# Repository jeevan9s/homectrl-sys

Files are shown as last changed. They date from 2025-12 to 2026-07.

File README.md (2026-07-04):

# homectrl

Home-automation controller with a Next.js dashboard. 

 ### Status
>- Controller PCB currently being manufactures
>- Firmware and **docs development** in progress.
>- Mechanical components currently being printed.

<details>
<summary><strong>Table of Contents</strong></summary>

- [homectrl](#homectrl)
    - [Status](#status)
  - [Overview](#overview)
  - [Features](#features)
    - [Controller](#controller)
    - [App](#app)
    - [Mechanical](#mechanical)
  - [Architecture](#architecture)
    - [Systems](#systems)
  - [Electrical](#electrical)
    - [Power System](#power-system)
    - [Microcontroller](#microcontroller)
    - [Pump Interface](#pump-interface)
    - [Stepper Motor Interface](#stepper-motor-interface)
    - [Peripheral Devices](#peripheral-devices)
  - [Mechanical](#mechanical-1)
    - [Container](#container)
    - [Lid](#lid)
  - [Firmware](#firmware)
  - [Web-App](#web-app)
  - [Repository Structure](#repository-structure)
  - [Gallery](#gallery)

</details>

I built homectrl because I wanted to automate my first apartment. 

<table> 
  <tr> 
    <td width="50%"> 
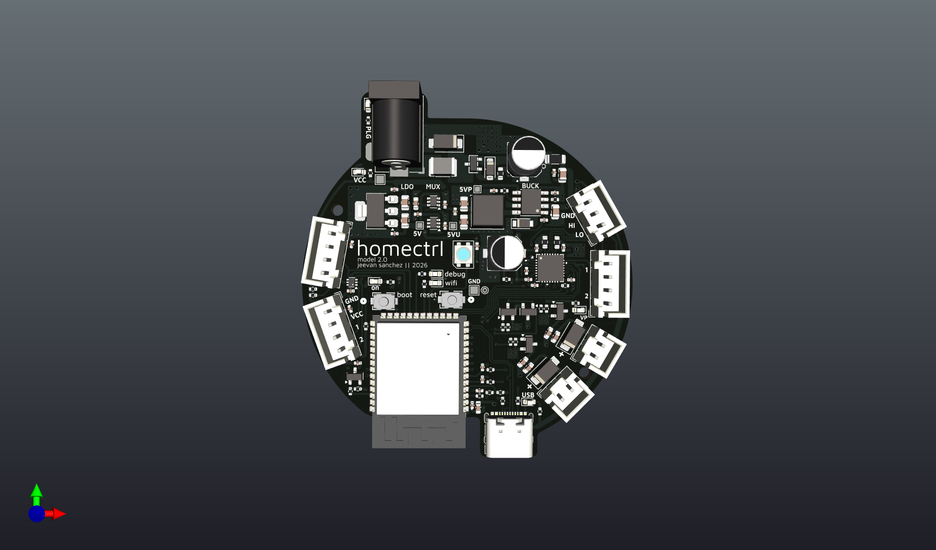
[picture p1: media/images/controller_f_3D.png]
       
    </td> 
    <td width="50%"> 
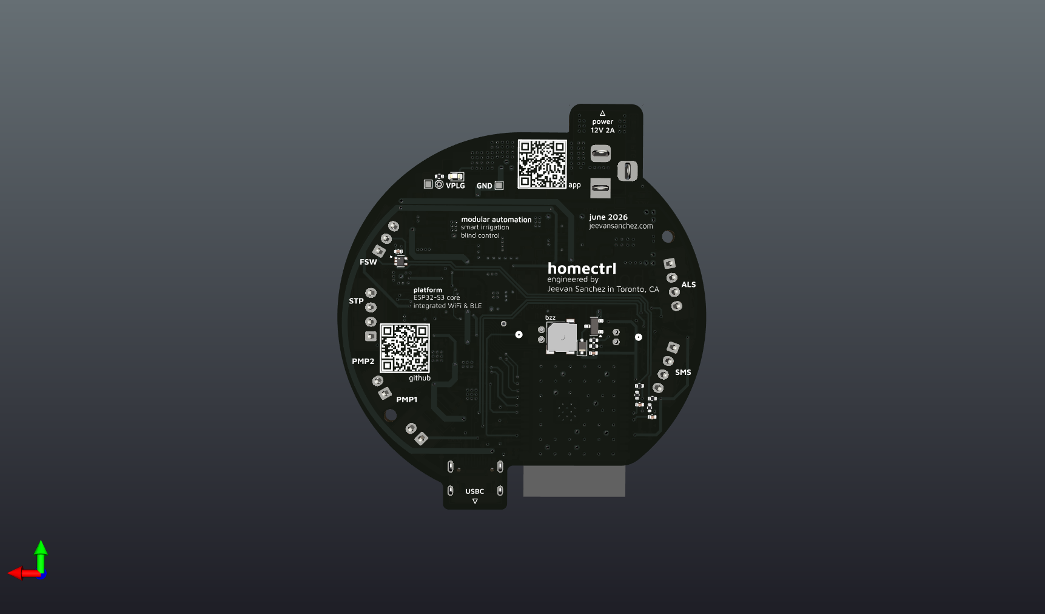
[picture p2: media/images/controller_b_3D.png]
       
    </td> 
  </tr> 
</table>

## Overview
Practicality is a consistent motive when building. 

As I moved into my first apartment during my first year at Queen's University, I wanted a device capable of smart-control for plants and window blinds, which are main components of my studio. This pushed me to build **homectrl**, a controller that leverages sensor readings, actuators, and WiFi for home automation. 

The first version was manufactured in October of 2025, and this was my first PCB designed. It was a bit elementary, lots of breakout boards soldered on, an MCU devkit, etc. 
Over the year I designed several other PCBs and learned a lot, which pushed me to produce a second version that I can use reliably for my 2nd year in Kingston. 

It's now June and the controller is being manufactured while I write docs and firmware. 

## Features 
### Controller

The controller is powered by a 12V 2A adapter and driven by an ESP32-S3.

Below is a list of features from power circuits to various peripherals. 
- Power-entry circuitry with OC/OV protetction, RPP, and PI-filter
- Regulation circuit featuring buck converter, 5V ORing, and LDO for logic power (3V3) 
- ESP32-S3 breakout circuitry with USB differential routing, S3 boot mode selection and reset toggle. 
- Controlled power delivery via CMOS and PMOS for main pump and moisture sensor power. 
- Low-side switching for pump control. 
- Stepper motor driven by TMC2209 with UART for blind control. 
- Float switches for monitoring irrigation tank. 
- Analog soil moisture sensor connectors with local RC filters. 
- ESD protection with TVS diode arrays on all external connections. 
- Visual and audible indication. 

### App

The controller communicates to a Next.js webapp via Websockets and is also connected to Alexa via SinricPro for voice control, over WiFi/MQTT.

- Next.js dashboard with modern responsive shadCN-tailwindcss UI. 
- Slider and switch control via UI. 
- Voice control with Alexa via SinricPro

### Mechanical 
- Lightweight container with USB and power ports and slots for cable management.
- Vents for airflow and audible indication. 
- Magnetic joints for easy lid removal and secure operation. 

## Architecture 
### Systems 

## Electrical 

This section provides low-level explanations of the significant circuits of each "module" of the controller.

I encourage you to clone the repo or you use [KiCanvas](https://kicanvas.org/) to look at the schematic and board files. 

All electronics were designed with **KiCad**.

### Power System

**Power Entry**
<p align="center">
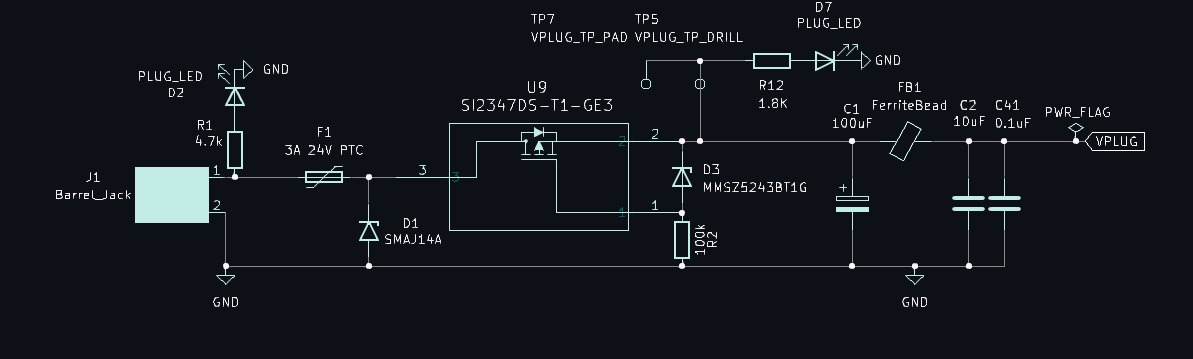
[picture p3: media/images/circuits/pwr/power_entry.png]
  
</p>

The 12V 2A power enters through a barrel jack connector, where it is then met with a 24V 3A fuse for over-current protection. A PTC resettable fuse was selected for durability. 

The positive plug line `VPLUG` is then protected from voltage spikes with a Transient Voltage Supression (TVS) diode placed in paralell for clamping. 
- The diode's standoff @ `14V`
- Breakdown @ `15.3V`
- Clamps @ `23.2V`

The positive line then goes through a Reverse Polarity Protection (RPP) circuit, using a P-Channel MOSFET for lossless efficiency (lower V drop than standard diodes). 

A Zener diode and resistor is placed between the MOSFET's gate and source for gate over-voltage protection. 

A bulk electrolytic (100μF) capacitor, ferrite bead, and high-frequency (0.1μF) capacitor are then placed to create a third-order low pass filter (π-filter). 
- This is used to smooth voltage spikes and reduce EMI.

The ferrite bead was primariy selected for its saturation current and DCR. 

The approximate current draw with safety margin $I_{net}$ is 2A.

$I_{\mathrm{sat}} = 1.5 \times I_{\mathrm{net}} \approx 3 A$

Minimize heat dissipation. 

$DCR$ is 20Ω

$P_{heat} = DCR \times I_{\mathrm{sat}} \approx 0.06 W$

**Voltage Regulation (I)**
<p align="center">
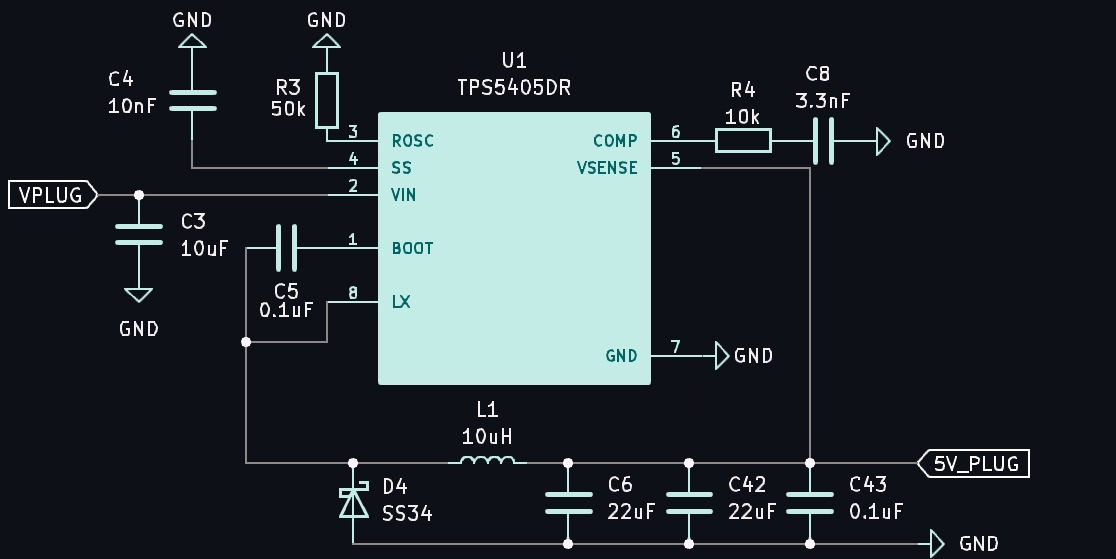
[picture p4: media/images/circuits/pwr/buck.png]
  
</p>

The controller uses a cascade regulation system, starting with the `TPS5405DR` buck converter. 

The input voltage is `VPLUG` (12V), after the protection and filtering circuitry, and the output is 5V. 

The $R_{osc}$ value will determine the switching frequency of the converter. 

Switching frequency is governed by the relationship. 
$$R_{\text{OSC}} (\text{k}\Omega) = 21.82 \cdot f_{\text{SW}}^{-1.167}$$

I chose a value of `50kΩ` for a $f_{SW}$ of approximately `525 kHz`

For the soft-start capacitor $C_{ss}$ , I chose a value of `10nF` for a soft-start time of `5ms`

The values below were taken from the [TPS5405DR Datasheet](https://www.ti.com/lit/gpn/tps5405)

$$
C_{SS} = \frac{t_{SS} \cdot I_{SS}}{V_{REF}}
$$

$$
C_{SS} = \frac{(5\,\mathrm{ms})(2\,\mathrm{\mu A})}{0.8\,\mathrm{V}}
= 12.5\,\mathrm{nF}
\approx 10\,\mathrm{nF}
$$

The inductor values were chosen using the equation below. 

$$
L=\frac{V_{out}\left(V_{in}-V_{out}\right)}
{V_{in}f_{sw}\Delta I_L}
$$

Using our calculated $f_{sw}$ from above and our voltage requirements (12V in, 5V out):
$$
L=
\frac{(5\,\mathrm{V})(12\,\mathrm{V}-5\,\mathrm{V})}
{(12\,\mathrm{V})(490\,\mathrm{kHz})(0.6\,\mathrm{A})}

\approx
10\,\mathrm{\mu H}
$$

The Schottky diode is rated for the `2A` output current and `12V`

**5V ORing**
<p align="center">
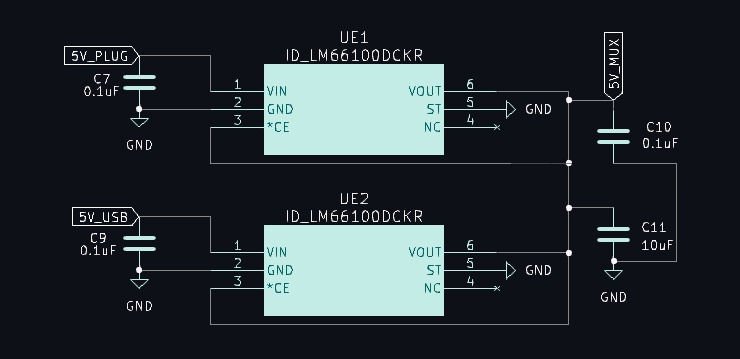
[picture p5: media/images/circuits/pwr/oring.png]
  
</p>

The `5V` rails from both USB and the buck converter are combined using an OR-ing circuit (Dual Ideal Diodes) to prevent backfeeding before feeding the second stage of regulation.

In this configuration, the outputs of both `LM66100` ideal diode controllers are tied together to form the shared `5V` rail. The `CE` pins of each device are also tied to the output rail, ensuring both controllers are only enabled once the rail is present 

This allows for testing over serial with devices that are powered by `VPLUG` (12V). 

**Voltage Regulation (II)**
<p align="center">
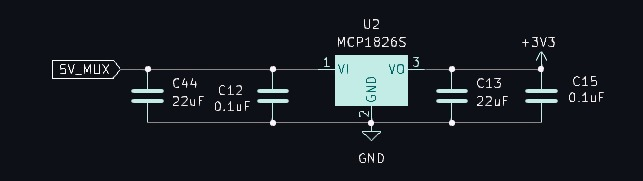
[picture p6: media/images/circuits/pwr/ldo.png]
  
</p>

The second stage of voltage regulation involes a Low-Dropout Regulator (LDO), the `MCP1826S`

It is fed the combined `5V` rail from the OR-ing circuit to produce the controller's logic-level voltage: `3V3`

**Controlled Pump Power Delivery**
<p align="center">
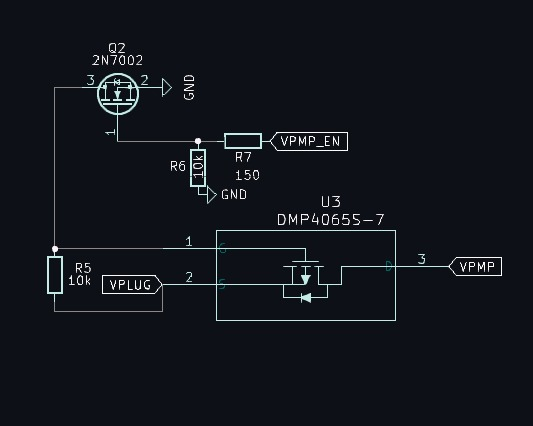
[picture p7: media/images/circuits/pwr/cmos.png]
  
</p>

The power for the pumps is controlled using a complementary-MOSFET (CMOS) setup, driven by a digital `HIGH` from the S3.

- When the control signal is low or floating, the N-channel MOSFET remains off and a pull-up resistor holds the gate of the P-channel MOSFET at the supply voltage, keeping it disabled and disconnecting the load rail.
- When the control signal is driven high, the N-channel MOSFET turns on and pulls the P-channel gate low, creating sufficient gate-source voltage to enable conduction and connect the supply to the load.

**Voltage Sensing**

A resistor divider circuit is used to produce a signal to be read by the S3's internal ADC.

- $R_1 = 100\,\mathrm{k\Omega}$
- $V_{plug} = 12\,\mathrm{V}$
- $V_{out} = 2\,\mathrm{V}$

$$
R_2 = \frac{R_1 \cdot V_{out}}{V_{batt} - V_{out}}
$$

$$
R_2 = \frac{100\,000 \cdot 2}{12 - 2}
= 20\,\mathrm{k\Omega}
$$

### Microcontroller
The controller is driven by an ESP32-S3-WROOM microcontroller.

**Digital IO**
<p align="center">
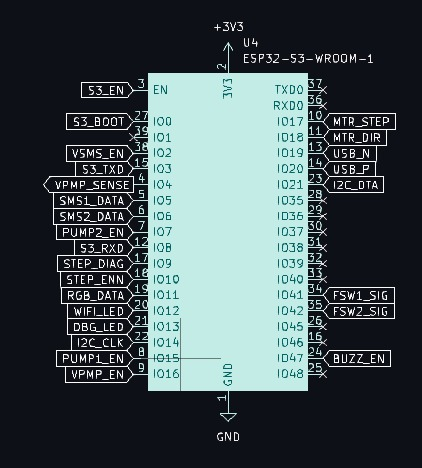
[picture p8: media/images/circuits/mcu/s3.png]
  
</p>

**Mode Select and Reset Toggle**
<p align="center">
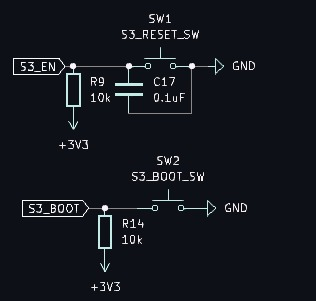
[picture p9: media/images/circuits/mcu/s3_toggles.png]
  
</p>

The S3 can be put into **BOOT** mode and **RESET** with onboard buttons.

**BOOT** mode determines whether the chip runs existing code from flash memory or waits to download new firmware.
- The ESP32 samples the **BOOT** pin (`GPIO0`) during reset to determine the boot mode.
- It is **active-low**: when pulled to **GND** during reset, the chip enters UART bootloader mode for flashing firmware.
- The circuit uses a momentary push-button to **GND** and a `10kΩ` pull-up resistor to ensure a defined high state during normal operation.

| BOOT0 Level | Boot Mode |
|---|---|
| HIGH | Programming Mode |
| LOW | Memory Mode |

**RESET** controls the Enable (EN) pin which is the ON/OFF (reset) switch for the ESP32.
- It is **active-low**: when pulled to **GND** it turns off the chip, and when released, it restarts.
- The circuit consists of a momentary push-button, a pull-up resistor to ensure the chip is enabled by default, and a `1µF` capacitor to filter out button noise.

### Pump Interface

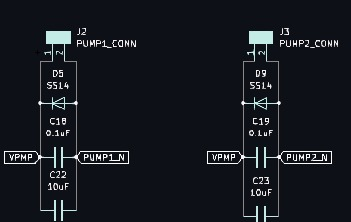
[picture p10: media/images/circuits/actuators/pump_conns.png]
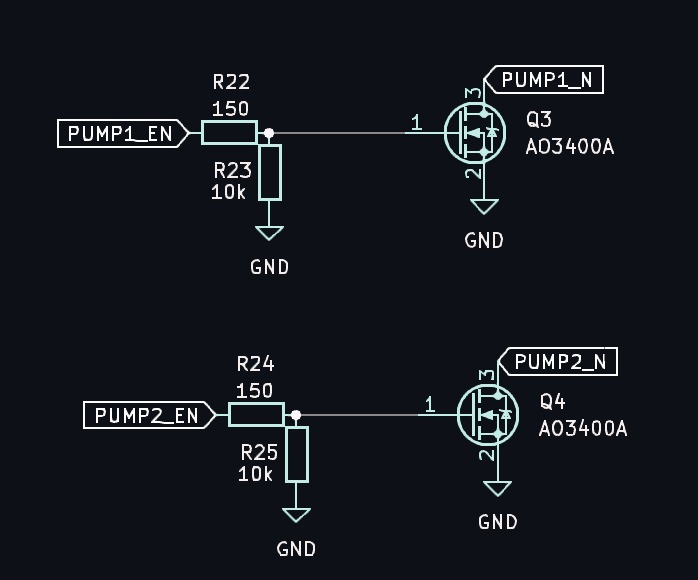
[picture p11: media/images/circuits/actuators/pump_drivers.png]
<table><tr><td width="50%"></td><td width="50%"></td></tr></table>

The controller interfaces with 12V 300mA rated pumps for irrigation. 

These pumps connect via JST-XH vertical headers and are met with flyback diodes for inductive spike protection, and decoupling to filter out noise. 

Each pump is controlled by a low-side switch using an `A03400A` N-channel MOSFET. 
- The gate of the MOSFET is driven by an S3 GPIO pin and is pulled down to GND for state definition. 
- The drain is connected to the negative terminal of the pump and the source to GND. 

This will bridge the negative pump terminal to GND and effectively turn it `ON` when the gate is `HIGH`. 

### Stepper Motor Interface
<p align="center">
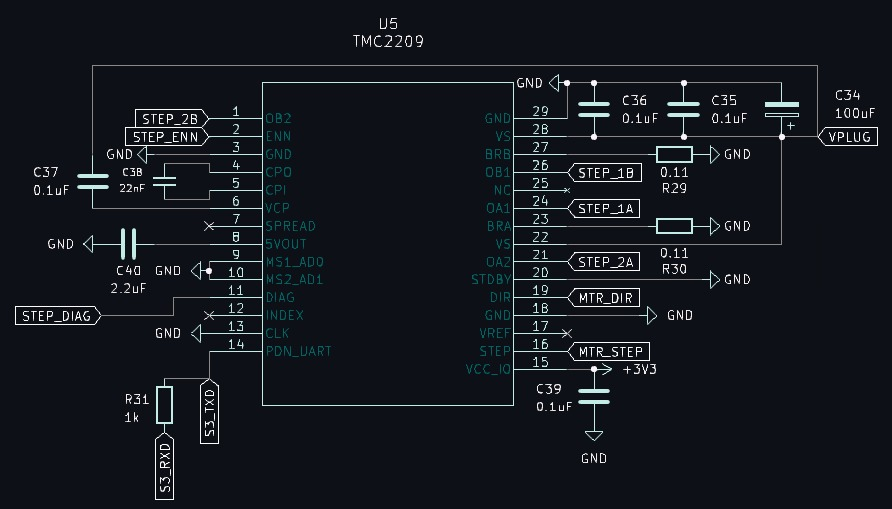
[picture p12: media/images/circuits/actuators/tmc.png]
  
</p>

The controller interfaces with a `NEMA 17` stepper motor through a `TMC2209` driver for blind control. 

The `NEMA 17` stepper motor connects via a vertical 4-position JST-XH header. 

The positive and negative terminals of both stepper coils feed the OBX and OAX pins of the driver. 

The driver is powered by `VPLUG` and is decoupled for bulk and high-frequency noise with electrolytic and ceramic capacitors. 
- The driver is put to sleep by the `ENN` pin to avoid power consumption, which is why I didn't use a CMOS/controlled-power delivery setup.

The main control signals are `STEP` and `DIR`, controlling the speed and direction, respectively. These connect digital pins on the S3. 

The single-wire UART interface was used for advanced chip config, live diagnostics, and features. 

The `BRA` and `BRB` connect to `0.11Ω` sense resistors to monitor and regulate current through the motor coils. 

For addressing, the `MS1_AD01` and `MS2_AD1` pins are pulled low to set the binary address bits to `00` and the UART slave address to `%0`. 

The `CP0` and `CP1` pins are tied together with a 22nF capacitor to generate a boost voltage for the internal charge pump. This boosted voltage switches the internal N-channel MOSFETs fully on. 

### Peripheral Devices

**Sensors**
<p align="center">

</p>

The controller interfaces with two capactive soil-moisture sensors (SMS) and an Ambient Light Sensor (ALS). 

These connections are made with vertical 4-pin JST-XH headers. 

I designed the ALS breakout board, in the future I'd be interested in designing the moisture sensors. For now I'm using the Adafruit models.

The `3V3` SMS power  is controlled through a simple `A03407A` P-channel mosfet, and the signals are filtered with a resistor-capacitor network at the S3 ADC pins. 

The ALS communicates with the `I2C` protocol and is powered by `3V3`. 

The two analog signals and I2C clock and data signals are ESD-protected by a `TPD43001` TVS diode array.

**Float Switches**
<p align="center">
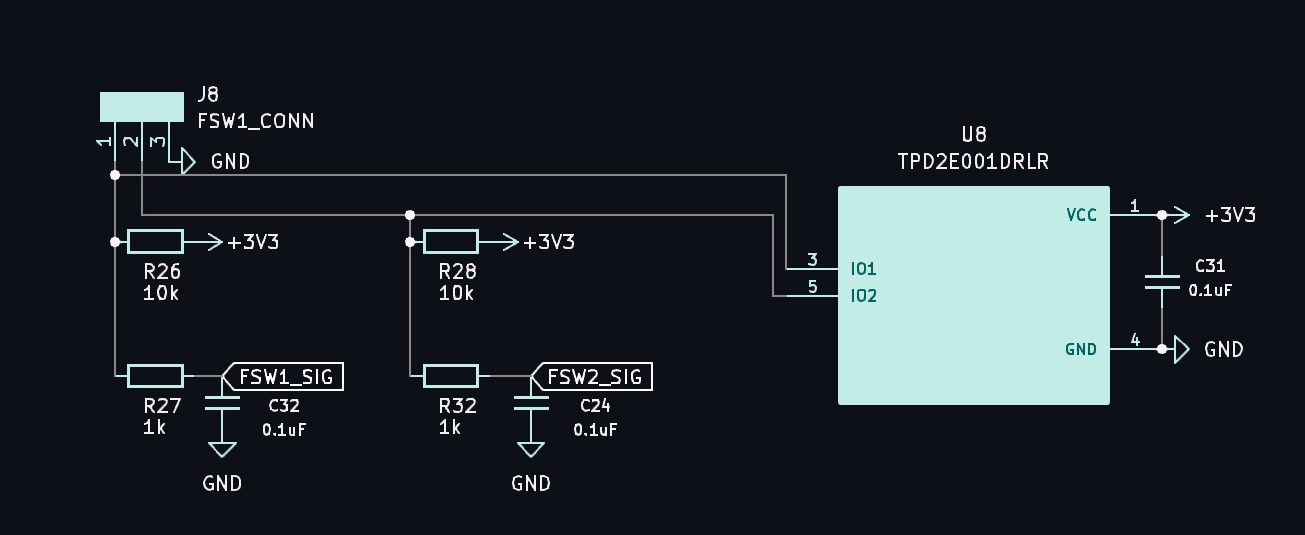
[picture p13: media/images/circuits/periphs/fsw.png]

</p>

The controller interfaces with two float switches. 

These connections are made with a vertical 3-pin JST-XH header. 

The signals are pulled up to 3V3 to establish a defined logic stateand filtered with a resistor-capacitor network at the S3 ADC pins. 

**Indicator Components**
- RGB LED
- Passive LEDs for simple indication
- Buzzer for audible indication

## Mechanical 
This section provides insight on the mechanical components of homectrl. 

I used Fusion360 to design everything.   

<p align="center">
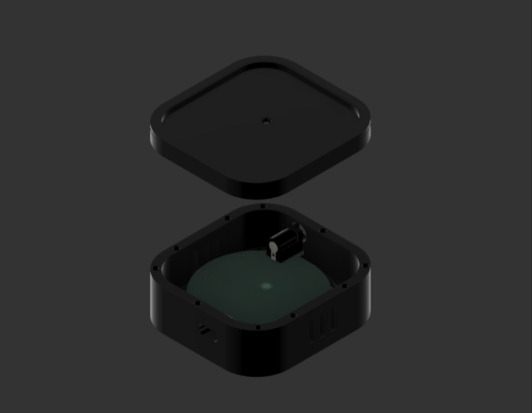
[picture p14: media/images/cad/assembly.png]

</p>

### Container
<p align="center">
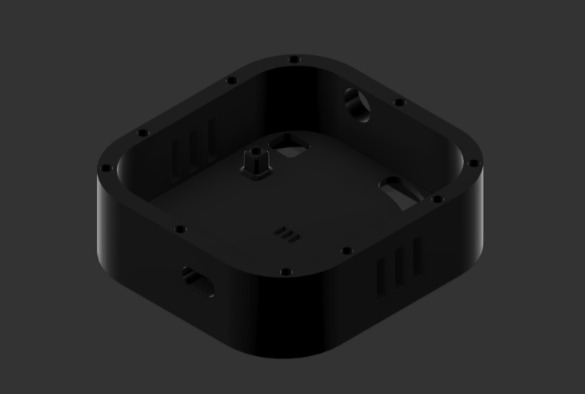
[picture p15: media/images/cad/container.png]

</p>

The container uses a rounded-rectangular exterior to house the board. 

The board is mounted using M2 standoffs designed from the base of the container. 

- It features USB-C and barrel-jack portholes for easy flashing and power connection.
- The backside has slot cutouts for actuator and sensor cables. 
- Vent holes were used throughout the container for airflow and weight management (more lightweight).

### Lid 
<p align="center">
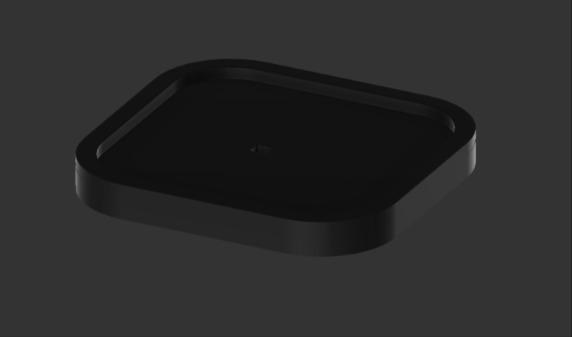
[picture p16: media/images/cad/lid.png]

</p>

The lid is mounted magnetically on the outer top face of the container using projected holes for small magnets. 
- Its design is honestly quite minimal, I did add a small hole for the controller's RGB LED to shine through. 

## Firmware

## Web-App

## Repository Structure 

## Gallery 

---
**huge thanks to PCBWay for sponsoring this project's first revision.**<br>
[check out **REV A**](https://github.com/jeevan9s/homectrl-sys/tree/rev-A)

---
Jeevan Sanchez, 2026

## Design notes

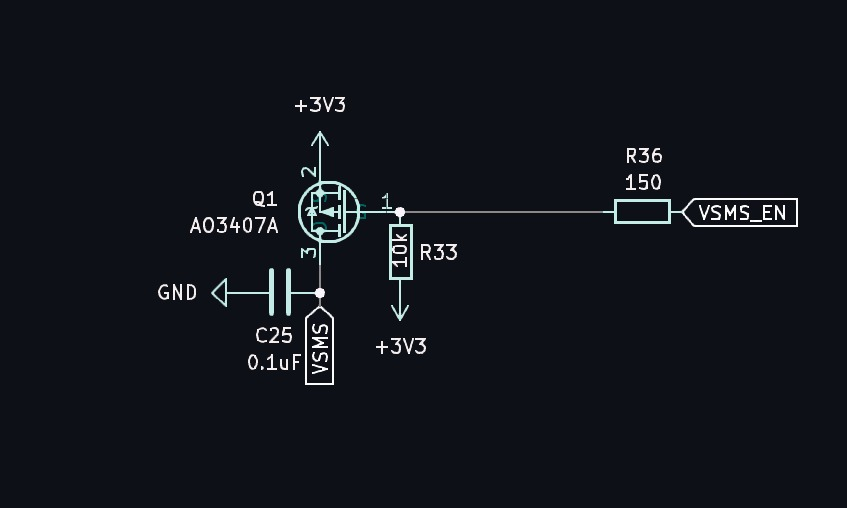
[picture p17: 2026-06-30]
media/images/circuits/pwr/pmos.png

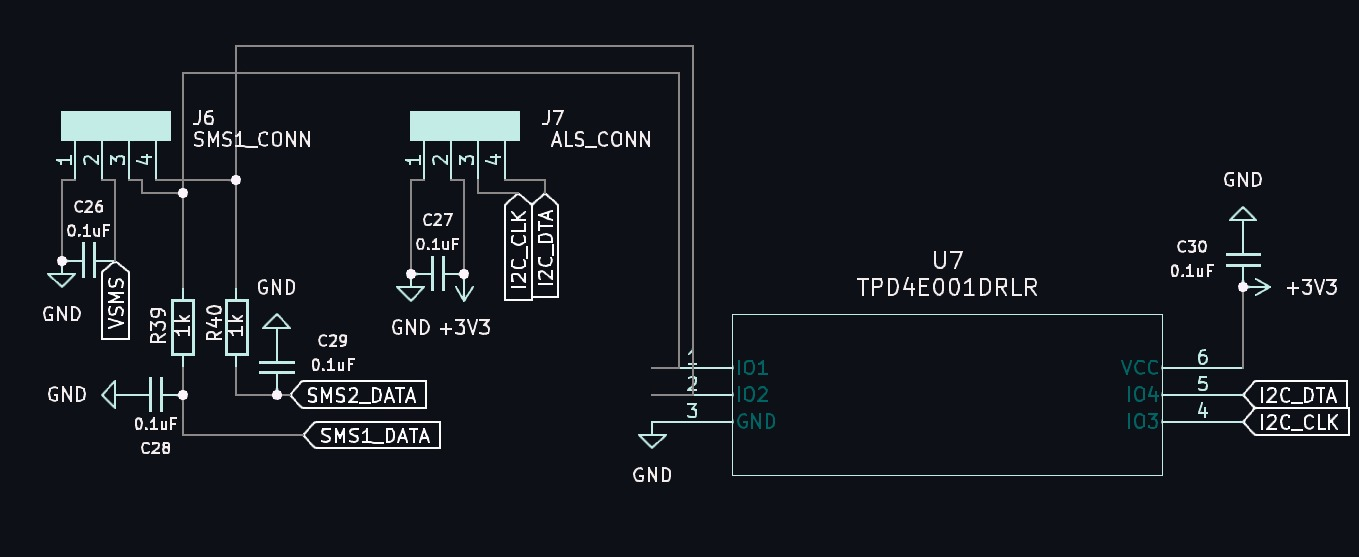
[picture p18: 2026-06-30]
media/images/circuits/periphs/sens.png

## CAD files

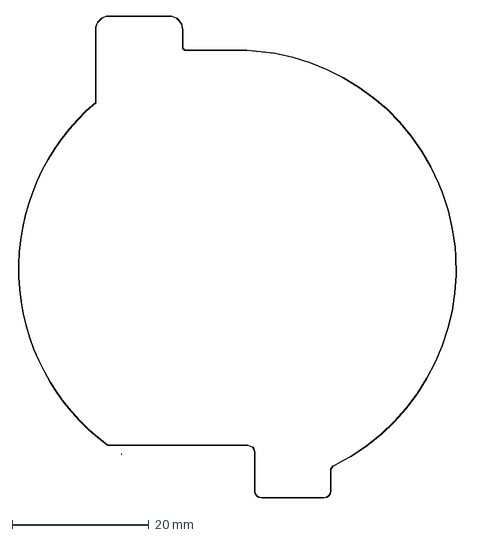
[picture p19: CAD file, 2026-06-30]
cad/board/homectrl_v2_board_outline.dxf
66.9 x 70.5 mm

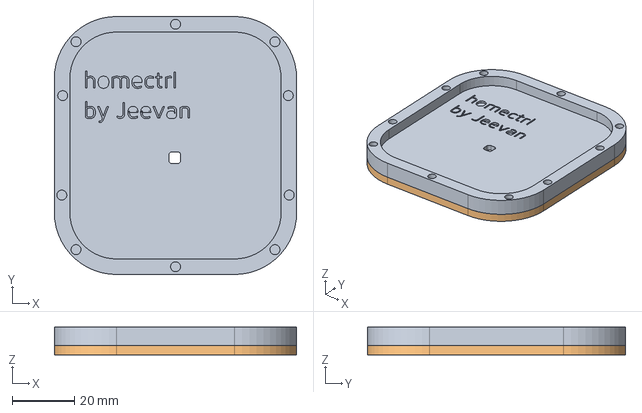
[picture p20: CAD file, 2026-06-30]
cad/container/container_lid.step
78.0 x 83.0 x 9.00 mm

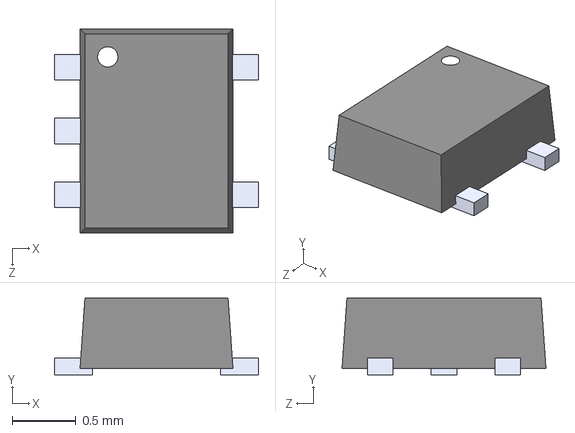
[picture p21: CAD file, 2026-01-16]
hardware/homectrl-rB/models/TPD2E001DRLR.step
1.60 x 0.6 x 1.60 mm

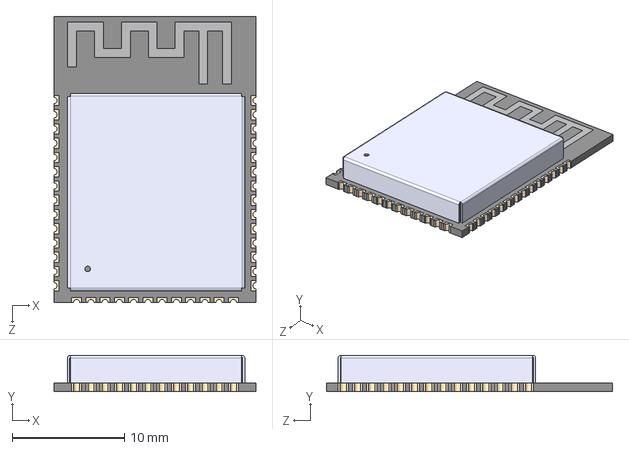
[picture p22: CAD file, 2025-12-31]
hardware/homectrl-v2/footprints/ESP32-S3-WROOM-1-N16R2/ESP32-S3-WROOM-1-N8R2--3DModel-STEP-56544.STEP
18.0 x 3.25 x 25.5 mm

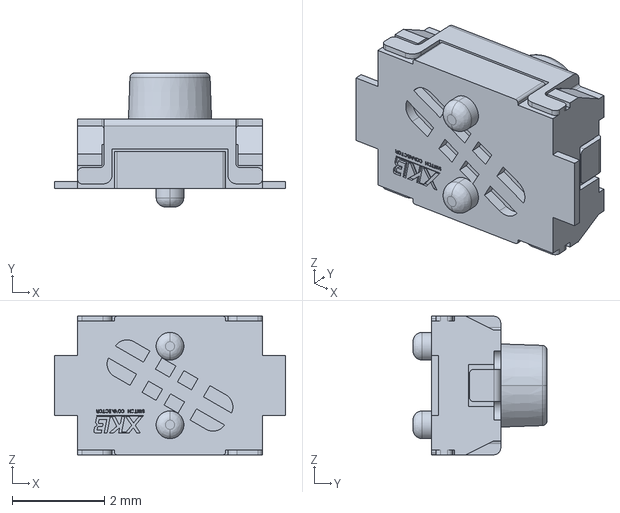
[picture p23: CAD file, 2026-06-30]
hardware/homectrl-v2/models/ts-1185-x-b-a-a.stp
5.00 x 2.90 x 3.00 mm

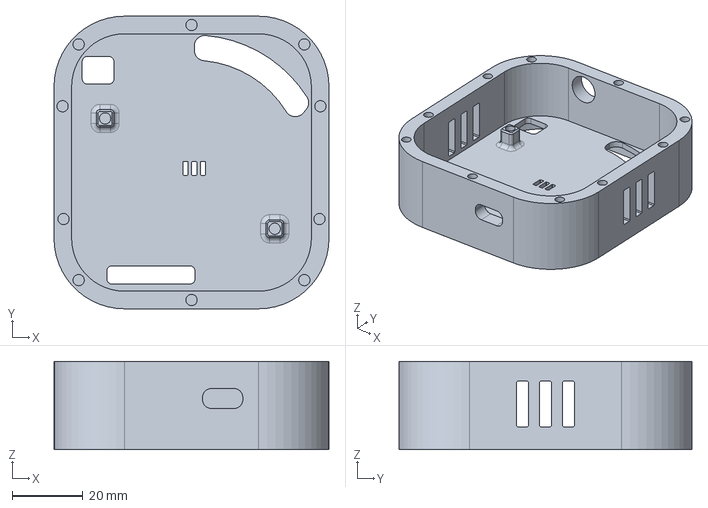
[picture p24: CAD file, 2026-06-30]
cad/container/container_base.step
78.0 x 83.0 x 25.0 mm

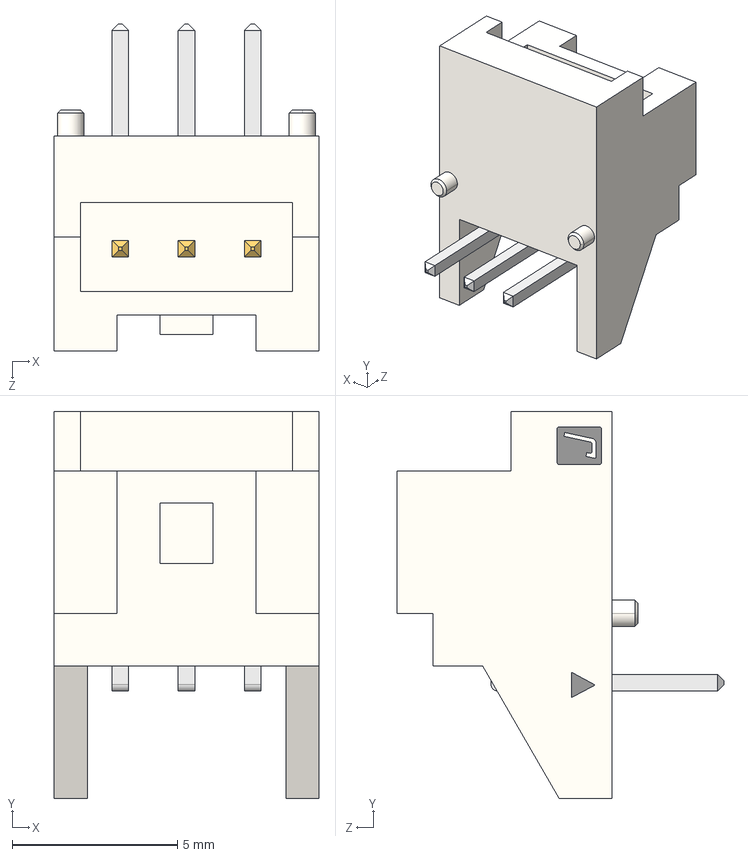
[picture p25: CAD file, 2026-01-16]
hardware/homectrl-rB/models/S03B-PASK-2_LF__SN_.stp
8.00 x 11.7 x 9.90 mm
S03B-PASK-2
JST Logo adjustable

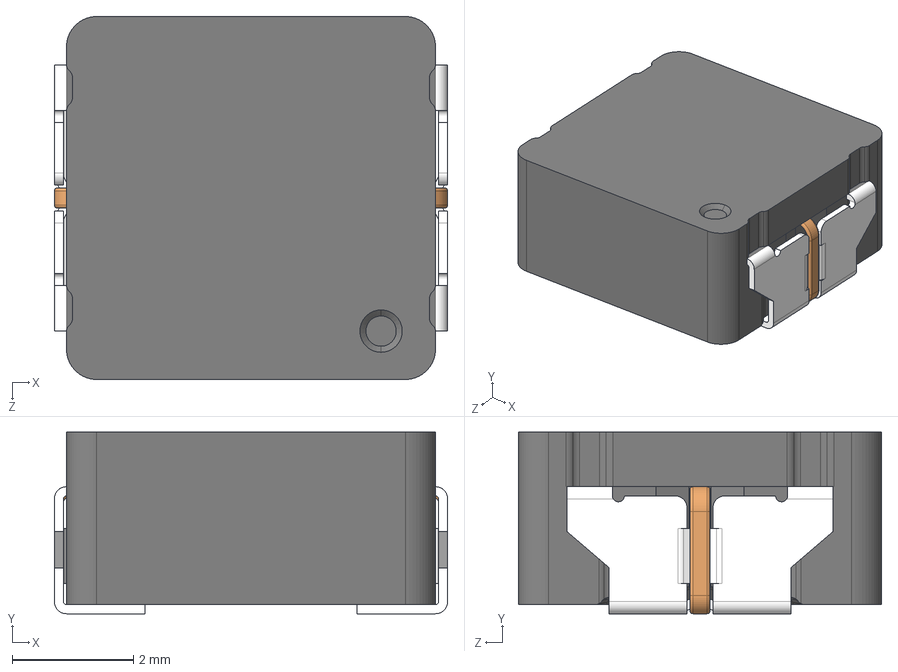
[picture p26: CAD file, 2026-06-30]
hardware/homectrl-v2/models/ETQP3M100HFN.step
6.50 x 3.00 x 6.00 mm

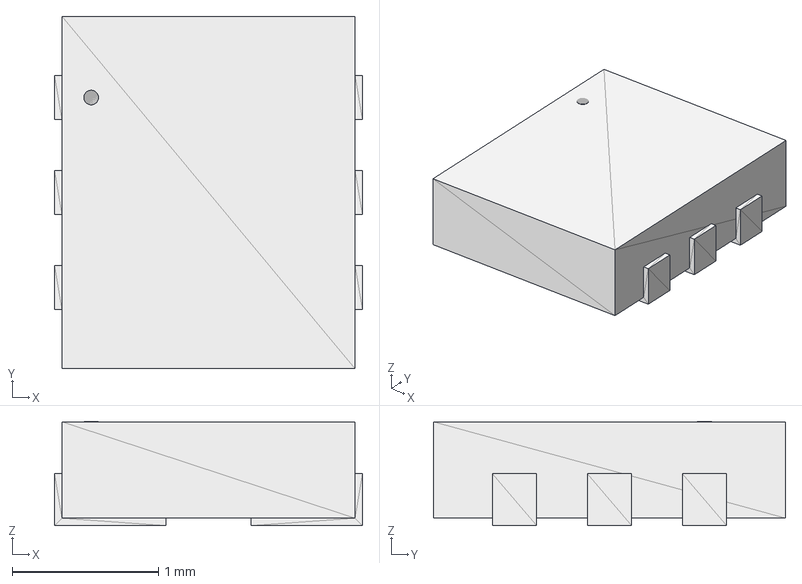
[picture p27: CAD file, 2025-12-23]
hardware/lux-module/models/lux-TSL2591.stp
2.11 x 2.41 x 0.714 mm

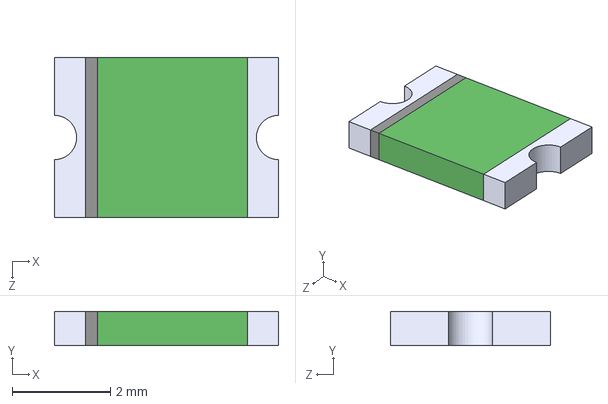
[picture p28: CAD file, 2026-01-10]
hardware/homectrl-rB/models/0ZCG0260BF2B.step
4.55 x 0.7 x 3.24 mm

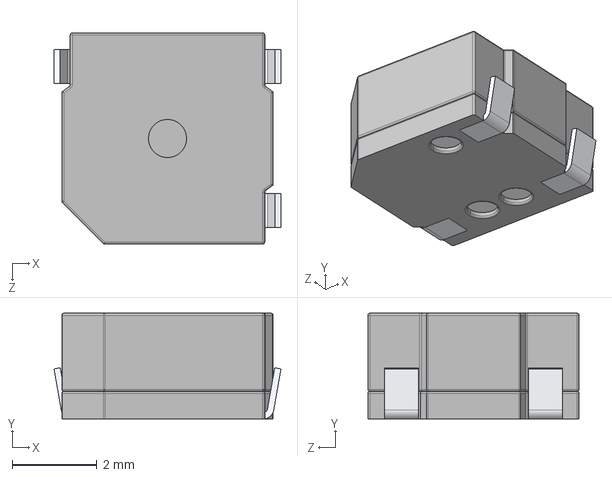
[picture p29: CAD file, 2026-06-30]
hardware/homectrl-v2/models/CMT-0525-75-SMT-TR.step
5.37 x 2.50 x 5.00 mm

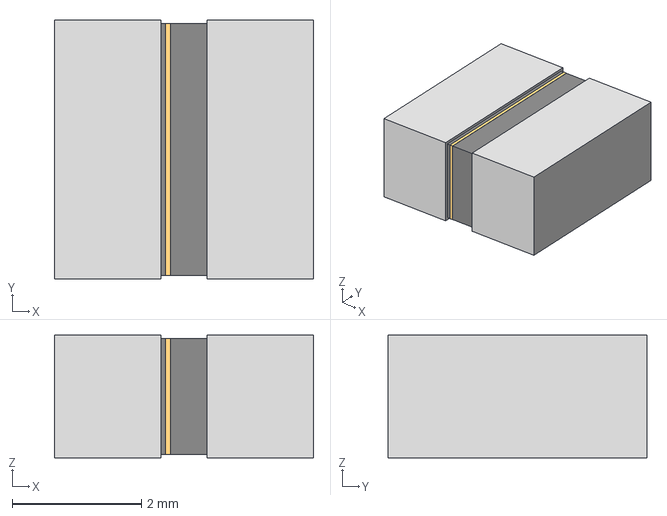
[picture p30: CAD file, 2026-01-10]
hardware/homectrl-rB/models/IND_IFSC_1515AH_VIS.step
4.01 x 4.01 x 1.91 mm

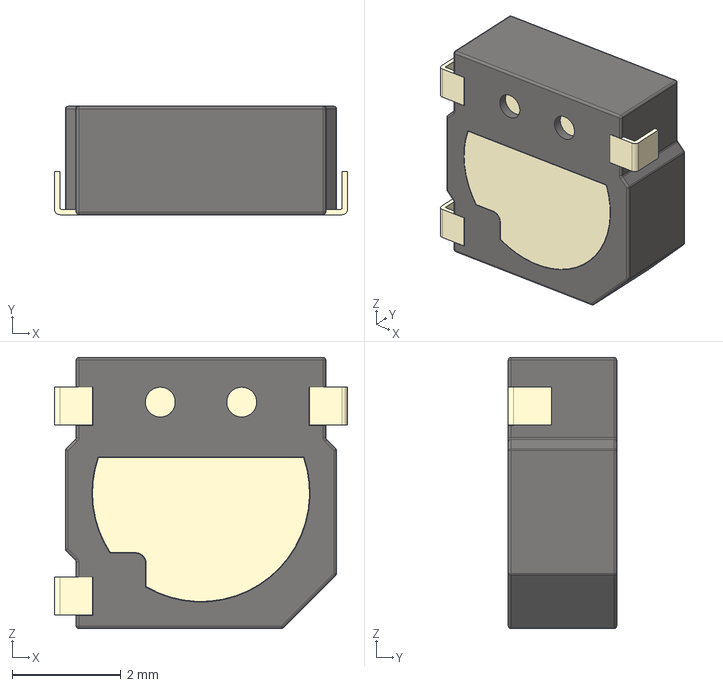
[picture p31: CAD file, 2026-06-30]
hardware/homectrl-v2/models/SMT-0540-S-R.step
5.40 x 2.00 x 5.00 mm

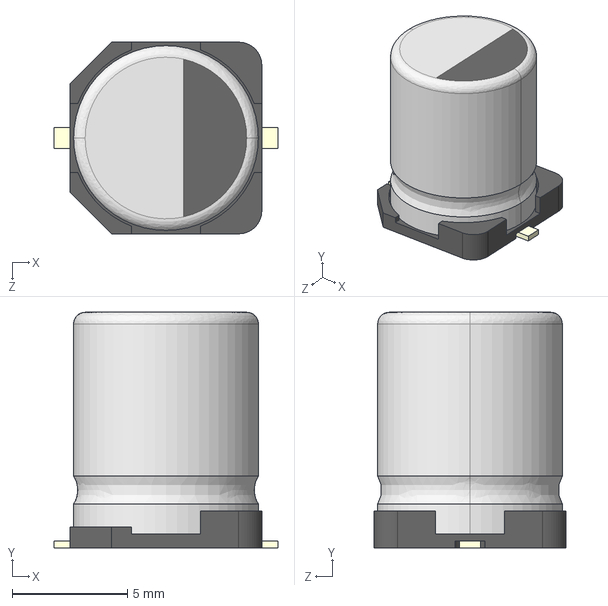
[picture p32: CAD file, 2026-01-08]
hardware/homectrl-rB/models/EEEFK1V101P.step
9.70 x 10.2 x 8.30 mm

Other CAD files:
hardware/homectrl-v2/models/S02B-PASK-2.stp
hardware/homectrl-rB/models/MPZ2012S221AT000.step
hardware/homectrl-v2/models/S04B-PASK-2.STEP
hardware/homectrl-rB/models/vls3015cx-1.step
hardware/homectrl-rB/models/530480310.stp
hardware/homectrl-rB/models/IN-PI20TBT5R5G5B.stp
hardware/homectrl-rB/models/IN-PI33TBTPRPGPB.step
hardware/homectrl-rB/models/LM3940IMP-3.3_NOPB.step
hardware/homectrl-rB/models/LM66100DCKR.STEP
hardware/homectrl-rB/models/QFN28_5X5_TRI.step
hardware/homectrl-rB/models/TO-236_VIS.step
hardware/homectrl-rB/models/TPS5405DR.step
hardware/homectrl-rB/models/VLS3015CX-220M-1.step
hardware/homectrl-v2/models/EEH-ZK1V101XP.step
hardware/lux-module/models/10118194-0001LF-USB.step

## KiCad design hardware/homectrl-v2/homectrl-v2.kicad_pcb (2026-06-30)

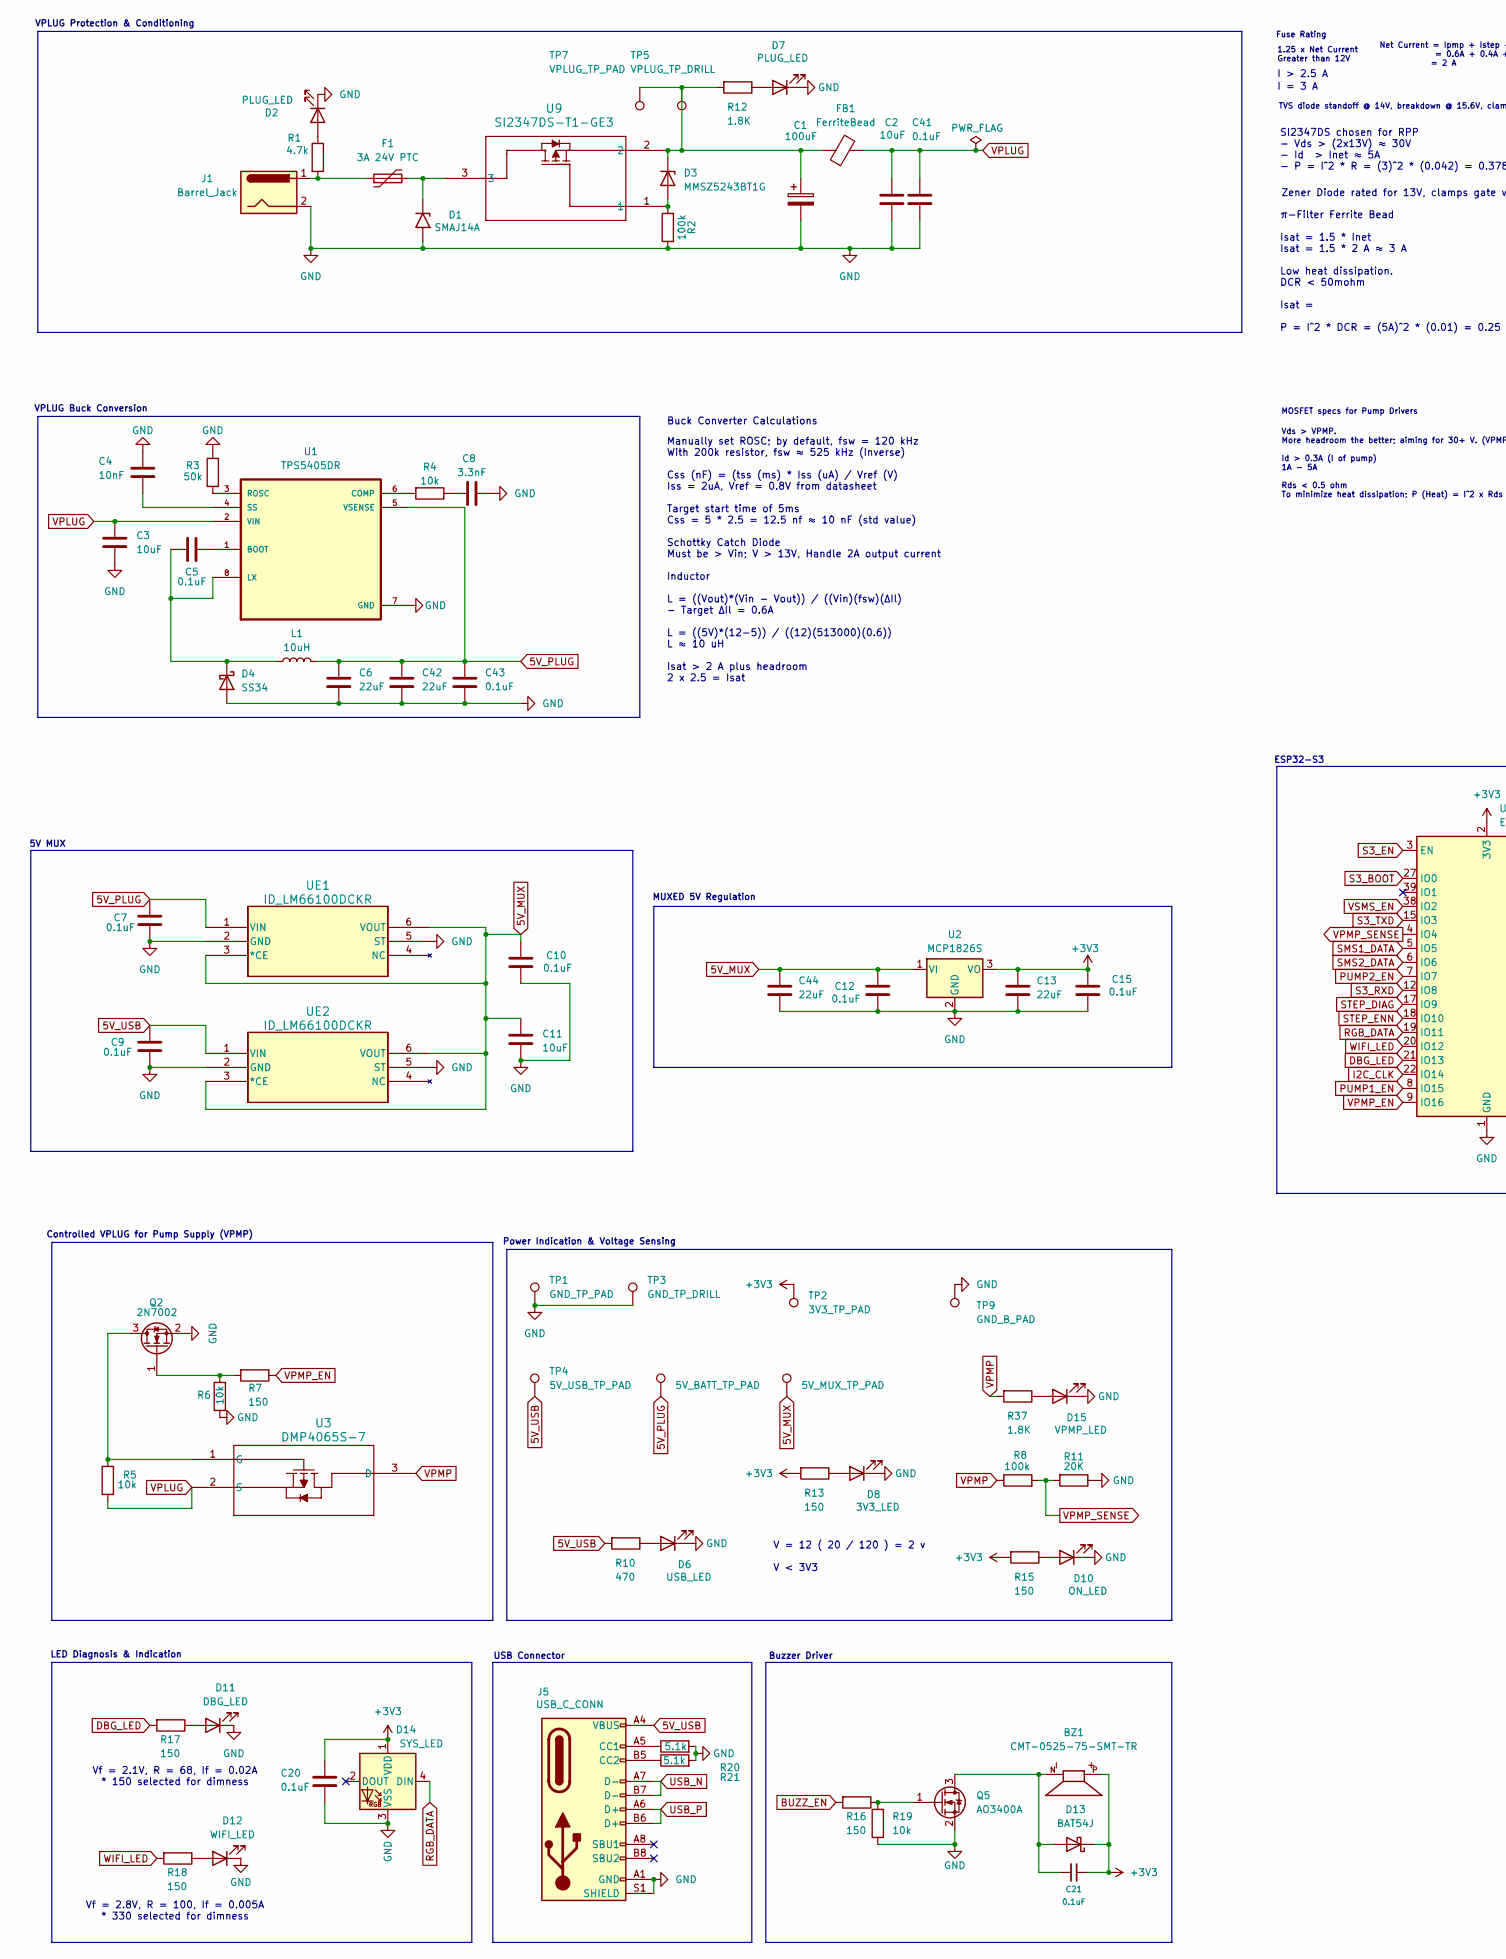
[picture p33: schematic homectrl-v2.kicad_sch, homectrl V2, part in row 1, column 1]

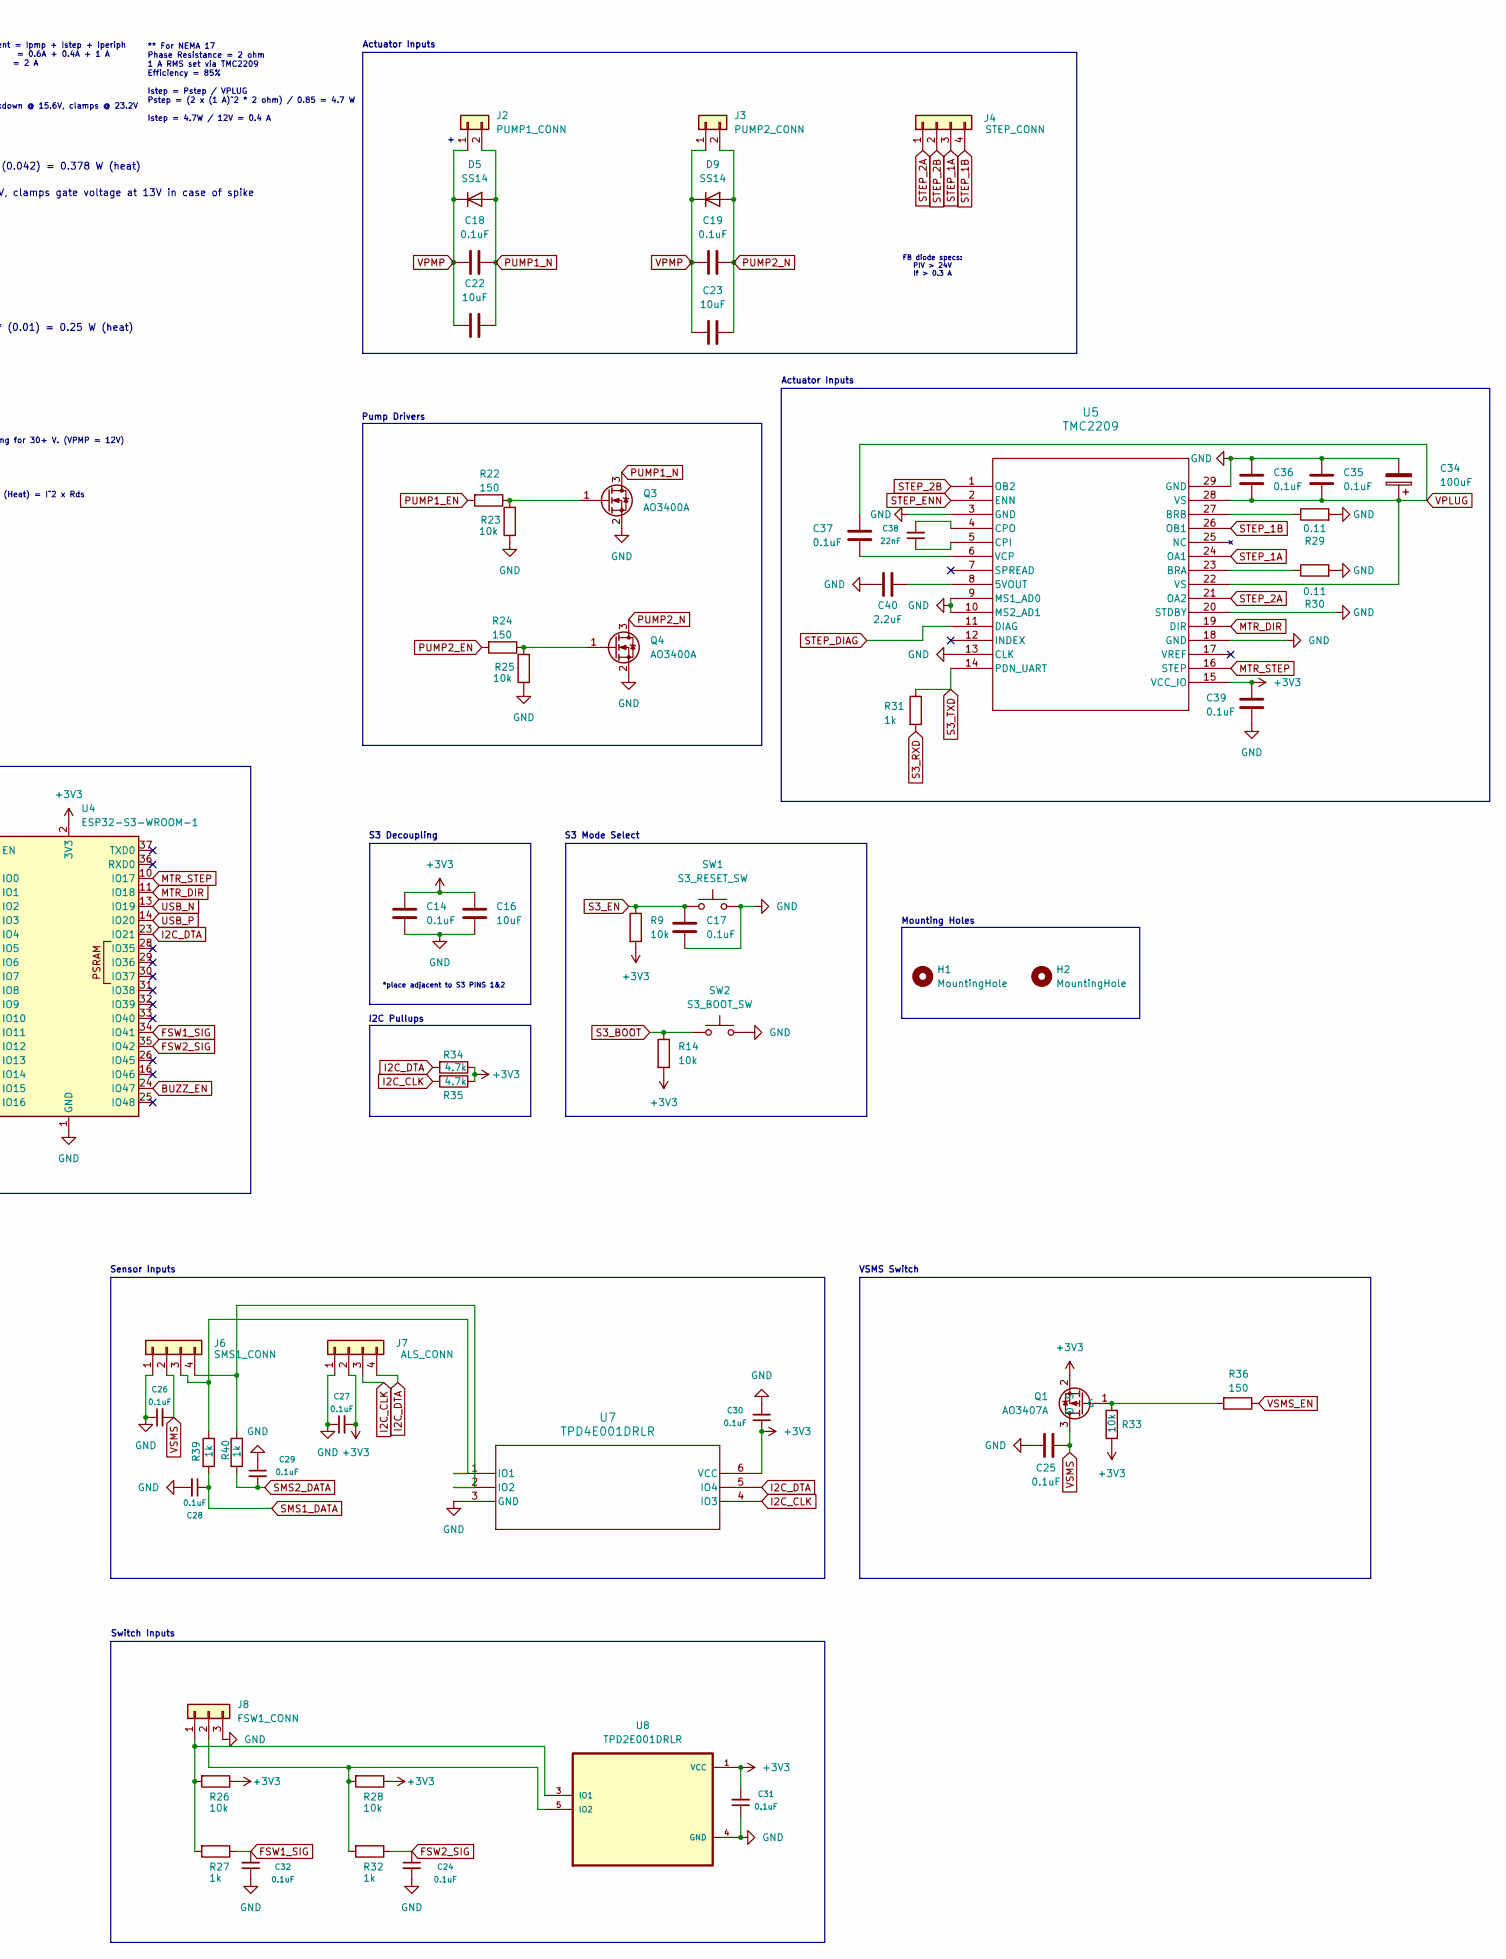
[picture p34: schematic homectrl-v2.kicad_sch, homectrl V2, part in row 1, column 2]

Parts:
BZ1: CMT-0525-75-SMT-TR; XDCR_CMT-0525-75-SMT-TR; PARTREV 1.0
C1: 100uF; CAP_EEHZK1V101XP; MPN EEE-FK1V101P
C2: 10uF; C_0805_2012Metric; MPN CL21A106KAYNNNE; LCSC C15850
C3: 10uF; C_0805_2012Metric; LCSC C15850
C4: 10nF; C_0402_1005Metric; LCSC C15195
C5, C7, C9, C10, C12, C14, C15, C17, C20, C21, C24, C25, C26, C27, C28, C29, C30, C31, C32, C35, C36, C37, C39, C41, C43: 0.1uF; C_0402_1005Metric; LCSC C77020
C6, C42: 22uF; C_0805_2012Metric; LCSC C45783
C8: 3.3nF; C_0402_1005Metric; LCSC C26404
C11, C16, C22, C23: 10uF; C_0603_1608Metric; LCSC C96446
C13, C44: 22uF; C_0805_2012Metric; LCSC C49326779
C18, C19: 0.1uF; C_0603_1608Metric; LCSC C14663
C34: 100uF; CAP_EEHZK1V101XP
C38: 22nF; C_0402_1005Metric; LCSC C1532
C40: 2.2uF; C_0402_1005Metric; LCSC C72203
D1: SMAJ14A; D_SMA
D2: PLUG_LED; LED_0603_1608Metric; LCSC C2297
D3: MMSZ5243BT1G; D_SOD-123; LCSC C2856864
D4: SS34; Nexperia_CFP3_SOD-123W; LCSC C5380710
D5, D9: SS14; D_SMA
D6: USB_LED; LED_0603_1608Metric; LCSC C2297
D7: PLUG_LED; LED_0603_1608Metric; LCSC C12065
D8: 3V3_LED; LED_0603_1608Metric; LCSC C12065
D10: ON_LED; LED_0603_1608Metric; LCSC C2297
D11: DBG_LED; LED_0603_1608Metric; LCSC C72038
D12: WIFI_LED; LED_0603_1608Metric; LCSC C72041
D13: BAT54J; D_SOD-323F; LCSC C86299
D14: SYS_LED; LED_WS2812B-Mini_PLCC4_3.5x3.5mm; Digikey 1568-COM-16347CT-ND
D15: VPMP_LED; LED_0603_1608Metric; LCSC C12065
F1: 3A 24V PTC; Fuse_1812_4532Metric
FB1: FerriteBead; R_1206_3216Metric
H1, H2: MountingHole; MountingHole_2.2mm_M2
J1: Barrel_Jack; BarrelJack_Horizontal
J2: PUMP1_CONN; JST_XH_B2B-XH-A_1x02_P2.50mm_Vertical
J3: PUMP2_CONN; JST_XH_B2B-XH-A_1x02_P2.50mm_Vertical
J4: STEP_CONN; JST_XH_B4B-XH-A_1x04_P2.50mm_Vertical
J5: USB_C_CONN; USB_C_Receptacle_G-Switch_GT-USB-7010ASV; LCSC C5178541
J6: SMS1_CONN; JST_XH_B4B-XH-A_1x04_P2.50mm_Vertical
J7: ALS_CONN; JST_XH_B4B-XH-A_1x04_P2.50mm_Vertical
J8: FSW1_CONN; JST_XH_B3B-XH-A_1x03_P2.50mm_Vertical
L1: 10uH; L_Changjiang_FNR6045S; LCSC C360734
Q1: AO3407A; SOT-23; LCSC C15155
Q2: 2N7002; SOT-23; LCSC C8545
Q3, Q4, Q5: AO3400A; SOT-23; LCSC C20917
R1, R34, R35: 4.7k; R_0402_1005Metric; LCSC C22765
R2: 100k; R_0603_1608Metric; LCSC C1996
R3: 50k; R_0402_1005Metric; LCSC C166559
R4, R5, R6, R9, R14, R19, R23, R25, R26, R28, R33: 10k; R_0402_1005Metric; LCSC C25744
R7, R13, R15, R16, R17, R18, R22, R24, R36: 150; R_0402_1005Metric; LCSC C25082
R8: 100k; R_0402_1005Metric; LCSC C25741
R10: 470; R_0402_1005Metric; LCSC C174152
R11: 20K; R_0402_1005Metric; LCSC C22356231
R12, R37: 1.8K; R_0402_1005Metric; LCSC C174229
R20, R21: 5.1k; R_0402_1005Metric; LCSC C25905
R27, R31, R32, R39, R40: 1k; R_0402_1005Metric; LCSC C11702
R29, R30: 0.11; R_0603_1608Metric; LCSC C247140
SW1: S3_RESET_SW; SW_5-B-B-B-A_XKB; LCSC C561521
SW2: S3_BOOT_SW; SW_5-B-B-B-A_XKB; LCSC C561521
TP1: GND_TP_PAD; TestPoint_Pad_1.5x1.5mm
TP2: 3V3_TP_PAD; TestPoint_Pad_1.5x1.5mm
TP3: GND_TP_DRILL; TestPoint_THTPad_D1.0mm_Drill0.5mm
TP4: 5V_USB_TP_PAD; TestPoint_Pad_1.0x1.0mm
TP5: VPLUG_TP_DRILL; TestPoint_THTPad_D1.0mm_Drill0.5mm
TP6: 5V_BATT_TP_PAD; TestPoint_Pad_1.0x1.0mm
TP7: VPLUG_TP_PAD; TestPoint_Pad_1.0x1.0mm
TP8: 5V_MUX_TP_PAD; TestPoint_Pad_1.0x1.0mm
TP9: GND_B_PAD; TestPoint_Pad_1.0x1.0mm
U1: TPS5405DR; SOIC127P599X175-8N; LCSC C488409
U2: MCP1826S; SOT-223-3_TabPin2; LCSC C638624
U3: DMP4065S-7; SOT-23; LCSC C182476
U4: ESP32-S3-WROOM-1; XCVR_ESP32-S3-WROOM-1-N16R2; LCSC C2913199
U5: TMC2209; QFN28_5X5_TRI; LCSC C2150710
U7: TPD4E001DRLR; Texas_R-PDSO-N6_DRL-6; LCSC C527516
U8: TPD2E001DRLR; SOT50P160X60-5N; DigiKey_Part_Number 296-21883-1-ND
U9: SI2347DS-T1-GE3; SOT_7DS-T1-GE3_VIS; LCSC C145002
UE1, UE2: ID_LM66100DCKR; SOT-363_SC-70-6; LCSC C2869734

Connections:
5V_MUX: C10.2, C11.2, C12.2, C44.1, TP8.1, U2.1 (VI), UE1.3 (*CE), UE1.6 (VOUT), UE2.3 (*CE), UE2.6 (VOUT)
5V_PLUG: C6.1, C7.2, C42.1, C43.1, L1.2, TP6.1, U1.5 (VSENSE), UE1.1 (VIN)
5V_USB: C9.1, J5.A4 (VBUS), J5.A9 (VBUS), J5.B4 (VBUS), J5.B9 (VBUS), R10.2, TP4.1, UE2.1 (VIN)
+3V3: BZ1.P, C13.1, C14.1, C15.2, C16.1, C20.1, C21.1, C27.2, C30.1, C31.2, C39.1, D13.1 (K), D14.1 (VDD), J7.2, Q1.2 (S), R9.2, R13.2, R14.2, R15.2, R26.1, R28.1, R33.1, R34.1, R35.1, TP2.1, U2.3 (VO), U4.2 (3V3), U5.15 (VCC_IO), U7.6 (VCC), U8.1 (VCC)
BUZZ_EN: R16.2, U4.24 (IO47)
DBG_LED: R17.2, U4.21 (IO13)
FSW1_SIG: C32.2, R27.1, U4.34 (IO41)
FSW2_SIG: C24.1, R32.1, U4.35 (IO42)
GND: C1.2, C2.1, C3.2, C4.1, C6.2, C7.1, C8.2, C9.2, C10.1, C11.1, C12.1, C13.2, C14.2, C15.1, C16.2, C17.2, C20.2, C24.2, C25.2, C26.1, C27.1, C28.2, C29.1, C30.2, C31.1, C32.1, C34.2, C35.1, C36.1, C39.2, C40.1, C41.2, C42.2, C43.2, C44.2, D1.2 (A2), D2.1 (K), D4.2 (A), D6.1 (K), D7.1 (K), D8.1 (K), D10.1 (K), D11.1 (K), D12.1 (K), D14.3 (VSS), D15.1 (K), J1.2, J5.A1 (GND), J5.A12 (GND), J5.B1 (GND), J5.B12 (GND), J5.S1 (SHIELD), J6.1, J7.1, J8.3, Q2.2 (S), Q3.2 (S), Q4.2 (S), Q5.2 (S), R2.1, R3.2, R6.1, R11.1, R19.1, R20.2, R21.2, R23.1, R25.1, R29.2, R30.2, SW1.2, SW2.2, TP1.1, TP3.1, TP9.1, U1.7 (GND), U2.2 (GND), U4.1 (GND), U4.40 (GND), U4.41 (GND), U5.3 (GND), U5.9 (MS1_AD0), U5.10 (MS2_AD1), U5.13 (CLK), U5.18 (GND), U5.20 (STDBY), U5.29 (GND), U7.3 (GND), U8.4 (GND), UE1.2 (GND), UE1.5 (ST), UE2.2 (GND), UE2.5 (ST)
I2C_CLK: J7.3, R35.2, U4.22 (IO14), U7.4 (IO3)
I2C_DTA: J7.4, R34.2, U4.23 (IO21), U7.5 (IO4)
MTR_DIR: U4.11 (IO18), U5.19 (DIR)
MTR_STEP: U4.10 (IO17), U5.16 (STEP)
unnamed: C8.1, R4.1
unnamed: D1.1 (A1), F1.2, U9.3
unnamed: D2.2 (A), R1.1
unnamed: D3.2 (A), R2.2, U9.1
unnamed: C1.1, D3.1 (K), FB1.1, R12.2, TP5.1, TP7.1, U9.2
unnamed: C5.1, D4.1 (K), L1.1, U1.8 (LX)
unnamed: D6.2 (A), R10.1
unnamed: D7.2 (A), R12.1
unnamed: D8.2 (A), R13.1
unnamed: D10.2 (A), R15.1
unnamed: D11.2 (A), R17.1
unnamed: D12.2 (A), R18.1
unnamed: BZ1.N, C21.2, D13.2 (A), Q5.3 (D)
unnamed: D15.2 (A), R37.1
unnamed: F1.1, J1.1, R1.2
unnamed: J5.A5 (CC1), R20.1
unnamed: J5.B5 (CC2), R21.1
unnamed: J6.3, R39.1, U7.1 (IO1)
unnamed: J6.4, R40.1, U7.2 (IO2)
unnamed: J8.1, R26.2, R27.2, U8.3 (IO1)
unnamed: J8.2, R28.2, R32.2, U8.5 (IO2)
unnamed: Q1.1 (G), R33.2, R36.2
unnamed: Q2.3 (D), R5.2, U3.1 (G)
unnamed: Q2.1 (G), R6.2, R7.2
unnamed: Q3.1 (G), R22.1, R23.2
unnamed: Q4.1 (G), R24.1, R25.2
unnamed: Q5.1 (G), R16.1, R19.2
unnamed: C5.2, U1.1 (BOOT)
unnamed: R4.2, U1.6 (COMP)
unnamed: R3.1, U1.3 (ROSC)
unnamed: C4.2, U1.4 (SS)
unnamed: C40.2, U5.8 (5VOUT)
unnamed: R30.1, U5.23 (BRA)
unnamed: R29.1, U5.27 (BRB)
unnamed: C38.1, U5.5 (CPI)
unnamed: C38.2, U5.4 (CPO)
unnamed: C37.2, U5.6 (VCP)
PUMP1_EN: R22.2, U4.8 (IO15)
PUMP1_N: C18.2, C22.2, D5.2 (A), J2.2, Q3.3 (D)
PUMP2_EN: R24.2, U4.7 (IO7)
PUMP2_N: C19.2, C23.2, D9.2 (A), J3.2, Q4.3 (D)
RGB_DATA: D14.4 (DIN), U4.19 (IO11)
S3_BOOT: R14.1, SW2.1, U4.27 (IO0)
S3_EN: C17.1, R9.1, SW1.1, U4.3 (EN)
S3_RXD: R31.2, U4.12 (IO8)
S3_TXD: R31.1, U4.15 (IO3), U5.14 (PDN_UART)
SMS1_DATA: C28.1, R39.2, U4.5 (IO5)
SMS2_DATA: C29.2, R40.2, U4.6 (IO6)
STEP_1A: J4.3, U5.24 (OA1)
STEP_1B: J4.4, U5.26 (OB1)
STEP_2A: J4.1, U5.21 (OA2)
STEP_2B: J4.2, U5.1 (OB2)
STEP_DIAG: U4.17 (IO9), U5.11 (DIAG)
STEP_ENN: U4.18 (IO10), U5.2 (ENN)
USB_N: J5.A7 (D-), J5.B7 (D-), U4.13 (IO19)
USB_P: J5.A6 (D+), J5.B6 (D+), U4.14 (IO20)
VPLUG: C2.2, C3.1, C34.1, C35.2, C36.2, C37.1, C41.1, FB1.2, R5.1, U1.2 (VIN), U3.2 (S), U5.22 (VS), U5.28 (VS)
VPMP: C18.1, C19.1, C22.1, C23.1, D5.1 (K), D9.1 (K), J2.1, J3.1, R8.1, R37.2, U3.3 (D)
VPMP_EN: R7.1, U4.9 (IO16)
VPMP_SENSE: R8.2, R11.2, U4.4 (IO4)
VSMS: C25.1, C26.2, J6.2, Q1.3 (D)
VSMS_EN: R36.1, U4.38 (IO2)
WIFI_LED: R18.2, U4.20 (IO12)

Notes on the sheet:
TVS diode standoff @ 14V, breakdown @ 15.6V, clamps @ 23.2V
Pump Drivers
S3 Decoupling
VPLUG Buck Conversion
Buck Converter Calculations
VPLUG Protection & Conditioning
π-Filter Ferrite Bead Isat = 1.5 * Inet Isat = 1.5 * 2 A ≈ 3 A Low heat dissipation. DCR < 50mohm Isat = P = I^2 * DCR = (5A)^2 * (0.01) = 0.25 W (heat)
Vf = 2.1V, R = 68, If = 0.02A * 150 selected for dimness
Vds > VPMP. More headroom the better; aiming for 30+ V. (VPMP = 12V) Id > 0.3A (I of pump) 1A - 5A Rds < 0.5 ohm To minimize heat dissipation; P (Heat) = I^2 x Rds
VSMS Switch
MUXED 5V Regulation
Controlled VPLUG for Pump Supply (VPMP)
5V MUX
FB diode specs: PIV > 24V If > 0.3 A
I = 3 A
I > 2.5 A
MOSFET specs for Pump Drivers
Switch Inputs
Vf = 2.8V, R = 100, If = 0.005A * 330 selected for dimness
S3 Mode Select
Mounting Holes
Zener Diode rated for 13V, clamps gate voltage at 13V in case of spike
Net Current = Ipmp + Istep + Iperiph = 0.6A + 0.4A + 1 A = 2 A
Power Indication & Voltage Sensing
ESP32-S3
Fuse Rating
Buzzer Driver
SI2347DS chosen for RPP - Vds > (2x13V) ≈ 30V - Id > Inet ≈ 5A - P = I^2 * R = (3)^2 * (0.042) = 0.378 W (heat)
** For NEMA 17 Phase Resistance = 2 ohm 1 A RMS set via TMC2209 Efficiency = 85% Istep = Pstep / VPLUG Pstep = (2 x (1 A)^2 * 2 ohm) / 0.85 = 4.7 W Istep = 4.7W / 12V = 0.4 A
V = 12 ( 20 / 120 ) = 2 v V < 3V3
Sensor Inputs
1.25 x Net Current Greater than 12V
I2C Pullups
Actuator Inputs
LED Diagnosis & Indication
*place adjacent to S3 PINS 1&2
USB Connector
Manually set ROSC; by default, fsw = 120 kHz With 200k resistor, fsw ≈ 525 kHz (Inverse) Css (nF) = (tss (ms) * Iss (uA) / Vref (V) Iss = 2uA, Vref = 0.8V from datasheet Target start time of 5ms Css = 5 * 2.5 = 12.5 nf ≈ 10 nF (std value) Schottky Catch Diode Must be > Vin; V > 13V, Handle 2A outpu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

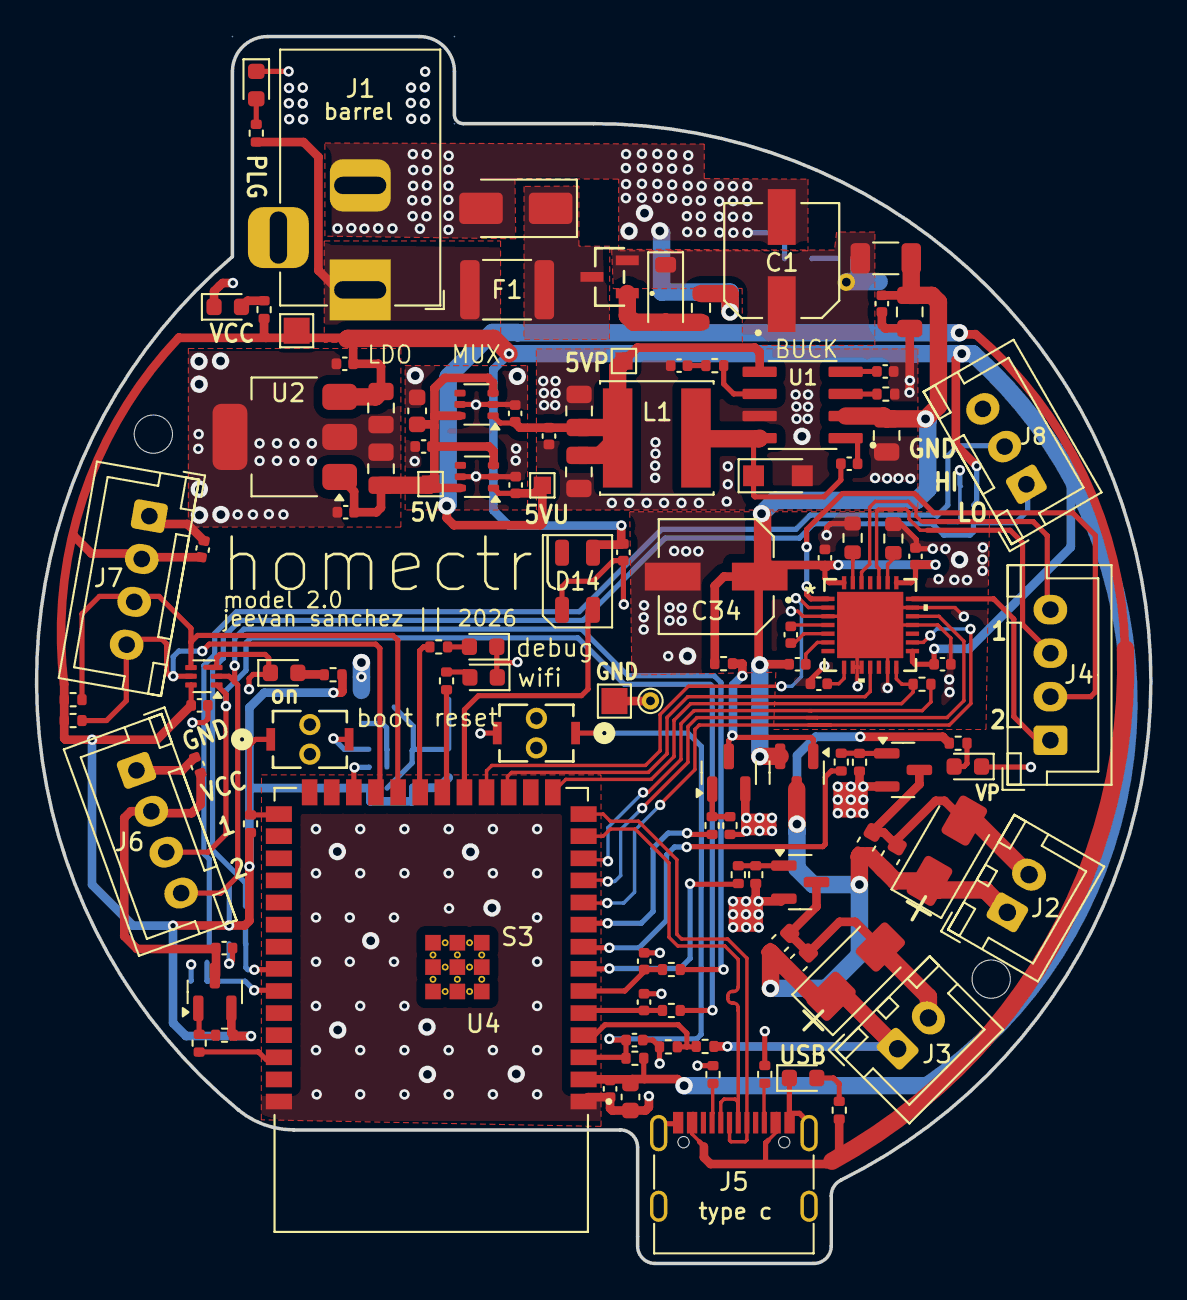
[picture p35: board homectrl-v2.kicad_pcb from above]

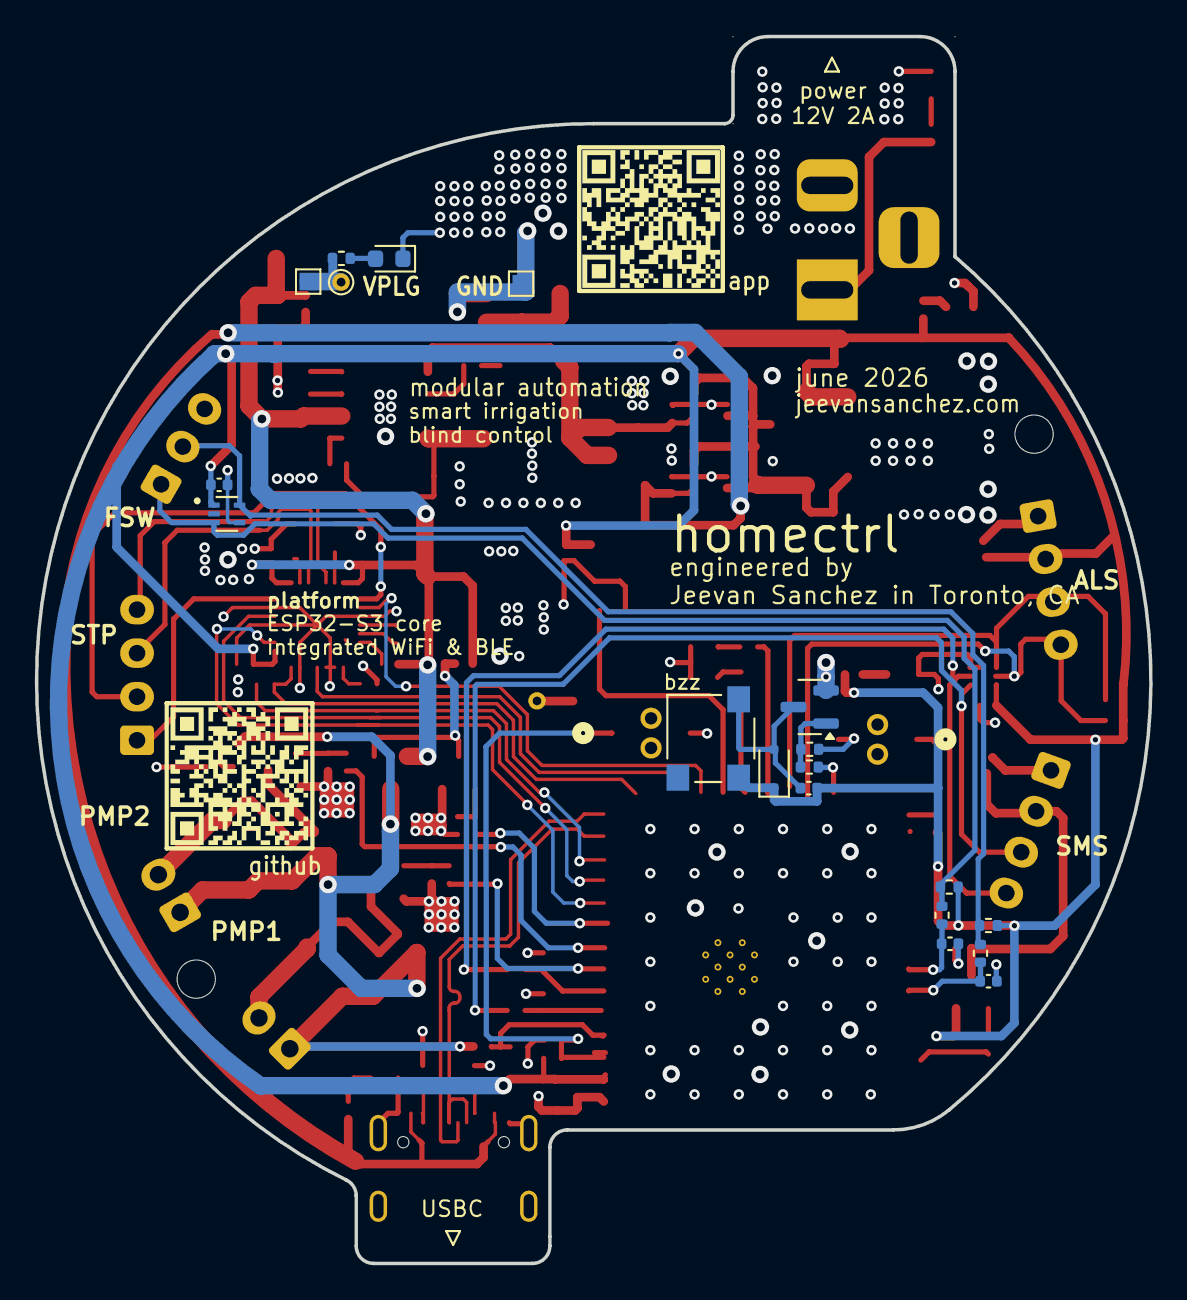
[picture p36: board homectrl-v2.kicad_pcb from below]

Board: 4 copper layers, 64.0 x 70.5 mm, 137 parts (19 on the bottom side), 76 nets.

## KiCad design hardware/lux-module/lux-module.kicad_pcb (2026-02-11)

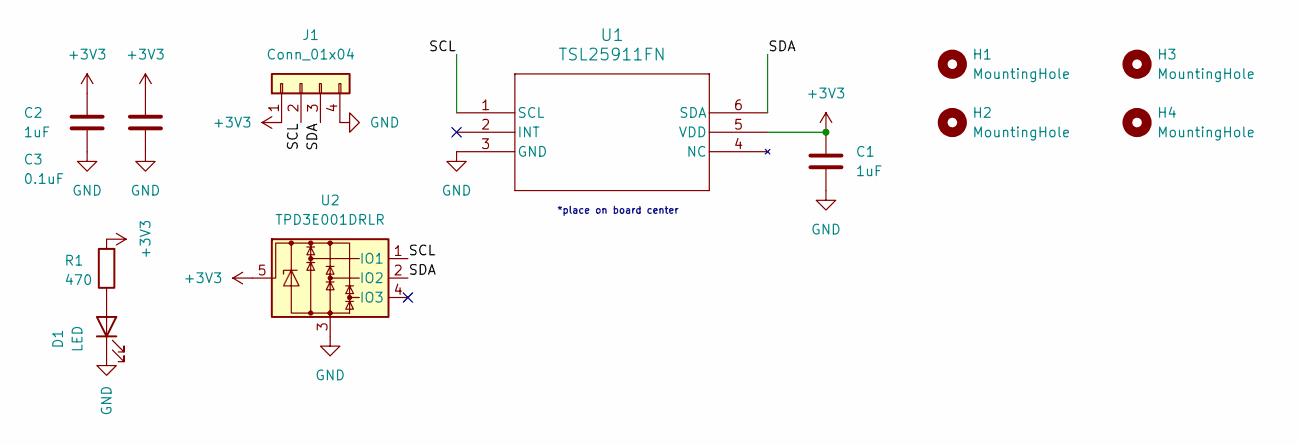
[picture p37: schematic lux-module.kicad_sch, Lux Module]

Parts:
C1: 1uF; C_0805_2012Metric; MPN C0805C104K5RACTU
C2: 1uF; C_0805_2012Metric; MPN CL21B106KOQNNNE
C3: 0.1uF; C_0805_2012Metric; MPN CL21B104KBCNNNC
D1: LED; LED_0603_1608Metric
H1, H2, H3, H4: MountingHole; MountingHole_2.2mm_M2; MPN N/A
J1: Conn_01x04; CONN4_S04B-PASK_JST; MPN S04B-PASK-2
R1: 470; R_0402_1005Metric
U1: TSL25911FN; lux-TSL2591; MPN TSL25911FN
U2: TPD3E001DRLR; SOT-553; MPN TPD3E001DRLR

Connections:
+3V3: C1.1, C2.1, C3.1, J1.1, R1.2, U1.5 (VDD), U2.5
/SCL: J1.2, U1.1 (SCL), U2.1 (IO1)
/SDA: J1.3, U1.6 (SDA), U2.2 (IO2)
GND: C1.2, C2.2, C3.2, D1.1 (K), J1.4, U1.3 (GND), U2.3
unnamed: D1.2 (A), R1.1

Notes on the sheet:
*place on board center

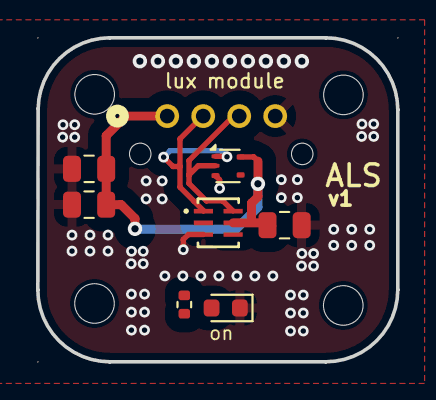
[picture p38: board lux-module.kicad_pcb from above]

Board: 2 copper layers, 20.0 x 18.0 mm, 12 parts (1 on the bottom side), 5 nets.

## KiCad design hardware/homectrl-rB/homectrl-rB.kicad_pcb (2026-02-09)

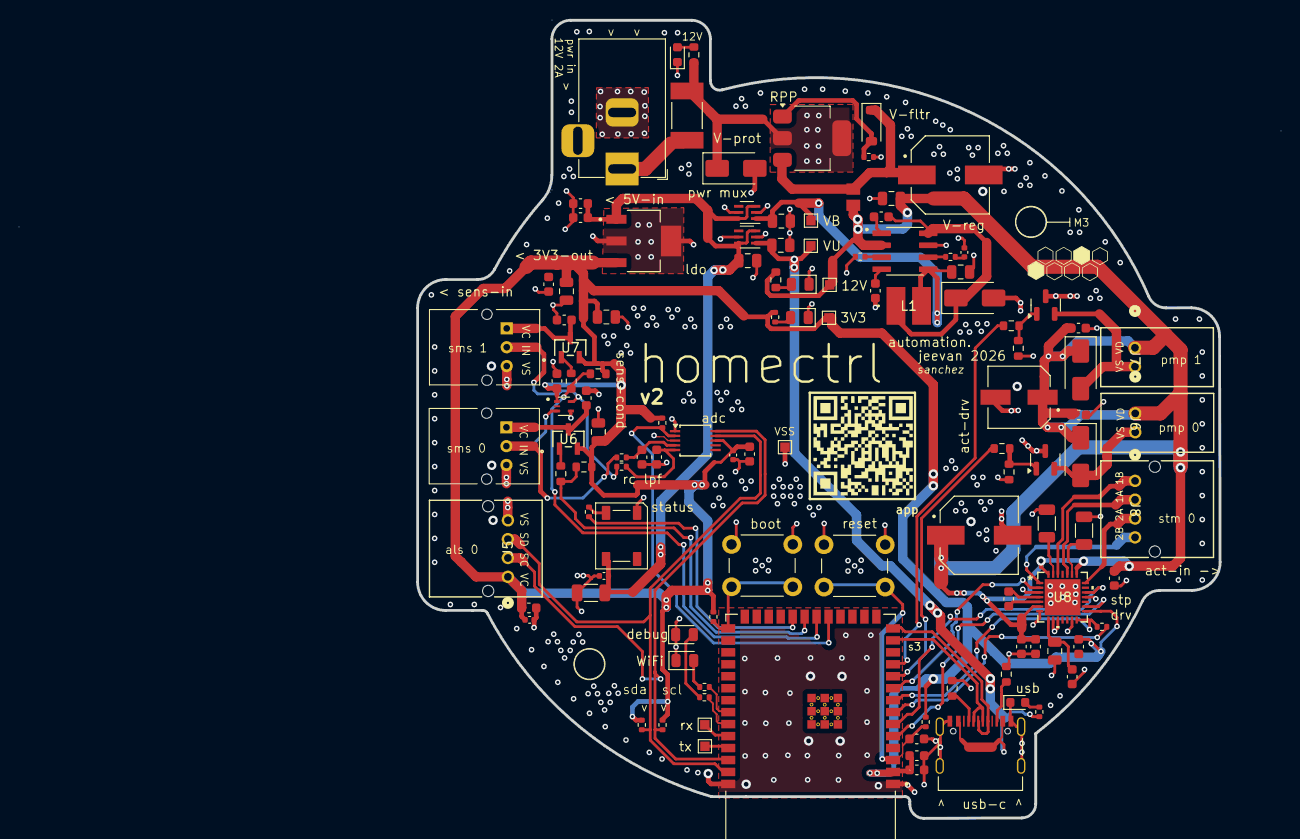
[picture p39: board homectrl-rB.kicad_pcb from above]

Board: 4 copper layers, 85.2 x 84.7 mm, 117 parts (0 on the bottom side), 67 nets.

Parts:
C1: 100uF; CAP_EEEFK1V101P
C2, C25, C26: 10uF; C_0805_2012Metric
C3: 47 nF; C_0603_1608Metric
C4: 3.3nF; C_0402_1005Metric
C5: 47nF; C_0603_1608Metric
C6, C9: 47uF; C_0805_2012Metric
C7: 0.47uF; C_0603_1608Metric
C8: 22uF; C_0805_2012Metric
C10, C16, C17, C19: 10uF; C_0603_1608Metric
C11, C12: 1uF; C_0805_2012Metric
C13, C14, C15, C21, C22, C23, C24, C28, C31, C32, C34, C35, C42, C43: 0.1uF; C_0603_1608Metric
C18, C20, C36: 0.1uF; C_0402_1005Metric
C27: 2.2uF; C_0603_1608Metric
C29: 22nF; C_0603_1608Metric
C30: 4.7uF; C_0805_2012Metric
C33: 220uF; CAP_EEEFK1V101P
C37: 10uF; C_1206_3216Metric
C41: 100uF; CAP_EEHZK1V101XP
D1: SS24; D_SMA
D2: SMAJ15A; D_SMA
D3: D_Zener; D_SOD-123
D4: 12V-LED; LED_0805_2012Metric
D5: 3V3-LED; LED_0805_2012Metric
D6: BUCK-LED; LED_0603_1608Metric
D7: SYS-LED; LED_WS2812B_PLCC4_5.0x5.0mm_P3.2mm
D8: WIFI-LED; LED_0805_2012Metric
D9: DEBUG-LED; LED_0805_2012Metric
D12: P0D; D_SMA
D13: P1D; D_SMA
D14: USB-LED; LED_0603_1608Metric
F1: Polyfuse; FUSER_0ZCG0260BF2B
FB1: FerriteBead; BEADC2012X105N
H1, H2: MountingHole; MountingHole_3.2mm_M3
J1: Barrel_Jack; BarrelJack_Horizontal
J2: USB_C_Female_USB2_Small; USB_C_DB-108PWB
J3: SMS-CONN-0; S03BPASK2LFSN
J4: SMS-CONN-1; S03BPASK2LFSN
J5: ALS_CONN; CONN4_S04B-PASK_JST
J6: PUMP0-CONN; CONN2_S02B-PASK-2_JST
J7: PUMP1-CONN; CONN2_S02B-PASK-2_JST
J8: STEP-CONN; CONN4_S04B-PASK_JST
L1: L; IND_IFSC_1515AH_VIS
Q1: DMP6023LE-13; SOT-223
Q2, Q3: AO3400A; SOT-23
R1: 15k; R_0402_1005Metric
R2, R3: 100k; R_0402_1005Metric
R4, R5: 4.7K; R_0603_1608Metric
R6, R15, R16, R27: 1k; R_0402_1005Metric
R7, R30: 330; R_0402_1005Metric
R8: 47; R_0402_1005Metric
R10, R11: 5.1k; R_0603_1608Metric
R12, R13, R14: 4.7k; R_0402_1005Metric
R17, R18, R21, R23: 1k; R_0603_1608Metric
R19, R20, R22, R24: 10k; R_0603_1608Metric
R25, R26: 0.11; R_1206_3216Metric
R28: 1.5k; R_0402_1005Metric
R29, R31: 10k; R_0402_1005Metric
SW1: SW_RESET; SW_PUSH_6mm
SW2: SW_BOOT; SW_PUSH_6mm
TP1: TX; TestPoint_Pad_1.0x1.0mm
TP2: RX; TestPoint_Pad_1.0x1.0mm
TP3: TP_5V-U; TestPoint_Pad_1.0x1.0mm
TP4: TP_12V; TestPoint_Pad_1.0x1.0mm
TP5: TP_3V3; TestPoint_Pad_1.0x1.0mm
TP6: TP-5V-B; TestPoint_Pad_1.0x1.0mm
TP7: TP-GND; TestPoint_Pad_1.0x1.0mm
U1: ESP32-S3-WROOM-1; XCVR_ESP32-S3-WROOM-1-N16R2
U2: TPS5405DR; SOIC127P599X175-8N
U3, U4: ID_LM66100DCKR; SC-70-6
U5: ADS1115IDGS; TSSOP-10_3x3mm_P0.5mm
U6, U7: SI2301; TO-236_VIS
U8: TMC2209; QFN28_5X5_TRI
U9: TPD2E001DRLR; SOT50P160X60-5N
VR1: LM3940IMP-3.3_NOPB; VREG_LM3940IMP-3.3_NOPB

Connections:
1A: J8.2, U8.24 (OA1)
1B: J8.1, U8.26 (OB1)
2A: J8.3, U8.21 (OA2)
2B: J8.4, U8.1 (OB2)
5V-B: C6.1, C11.1, L1.2, TP6.1, U2.5 (VSENSE), U3.1 (VIN)
5V-U: C12.1, J2.A4 (VBUS), J2.A9 (VBUS), J2.B4 (VBUS), J2.B9 (VBUS), R28.1, TP3.1, U4.1 (VIN)
+3V3: C8.2, C13.2, C14.2, C15.1, C16.1, C17.1, C18.1, C19.1, C20.1, C25.1, C26.1, C28.2, J5.1, R6.1, R12.2, R13.1, R14.1, R19.1, R20.1, R29.1, R31.1, TP5.1, U1.2 (3V3), U5.8 (VDD), U6.2 (S), U7.2 (S), U8.15 (VCC_IO), U9.1 (VCC), VR1.3 (OUT)
+5V: C7.2, C9.1, C10.2, C36.2, C37.2, D7.1 (VDD), U3.3 (*CE), U3.6 (VOUT), U4.3 (*CE), U4.6 (VOUT), VR1.1 (IN)
+12V: C2.2, C31.1, C32.1, C33.1, C34.2, C41.1, C42.1, C43.1, D12.1 (K), D13.1 (K), FB1.2, J6.1, J7.1, R5.1, TP4.1, U2.2 (VIN), U8.6 (VCP), U8.22 (VS), U8.28 (VS)
/ESP32-S3 Breakout/GPIO_14: R30.2, U1.22 (IO14)
/ESP32-S3 Breakout/GPIO_41: R8.1, U1.34 (IO41)
/ESP32-S3 Breakout/GPIO_42: R7.1, U1.35 (IO42)
ADC-RDY: R14.2, U1.19 (IO11), U5.2 (ALERT/RDY)
AOUT-0: J3.2, R16.1, U9.3 (IO1)
AOUT-1: J4.2, R15.1, U9.5 (IO2)
DIR: U1.6 (IO6), U8.19 (DIR)
EN: C35.1, R29.2, SW1.2, U1.3 (EN)
ENN: U1.9 (IO16), U8.2 (ENN)
GND: C1.2, C2.1, C4.2, C5.1, C6.2, C7.1, C8.1, C9.2, C10.1, C11.2, C12.2, C13.1, C14.1, C15.2, C16.2, C17.2, C18.2, C19.2, C20.2, C21.2, C22.1, C23.2, C24.2, C25.2, C26.2, C27.2, C28.1, C30.2, C31.2, C32.2, C33.2, C34.1, C35.2, C36.1, C37.1, C41.2, C42.2, C43.2, D1.2 (A), D2.2 (A2), D4.1 (K), D5.1 (K), D6.1 (K), D7.3 (VSS), D8.1 (K), D9.1 (K), D14.1 (K), J1.2, J2.A1 (GND), J2.A12 (GND), J2.B1 (GND), J2.B12 (GND), J2.S1 (SHIELD), J3.3, J4.3, J5.4, Q2.3, Q3.3, R2.2, R3.1, R10.2, R11.2, R22.1, R24.1, R25.2, R26.2, SW1.1, SW2.1, TP7.1, U1.1 (GND), U1.40 (GND), U2.7 (GND), U3.2 (GND), U3.5 (ST), U4.2 (GND), U4.5 (ST), U5.1 (ADDR), U5.3 (GND), U8.3 (GND), U8.7 (SPREAD), U8.9 (MS1_AD0), U8.10 (MS2_AD1), U8.13 (CLK), U8.18 (GND), U8.29 (GND), U9.4 (GND), VR1.2 (GND_2), VR1.4 (GND_4)
GPIO_0: R31.2, SW2.2, U1.27 (IO0)
unnamed: C4.1, R1.2
unnamed: C3.1, D1.1 (K), L1.1, U2.8 (LX)
unnamed: D2.1 (A1), F1.2, Q1.2 (D), R4.2
unnamed: D3.2 (A), Q1.1 (G), R2.1
unnamed: C1.1, D3.1 (K), FB1.1, Q1.3 (S)
unnamed: D4.2 (A), R5.2
unnamed: D5.2 (A), R6.2
unnamed: D6.2 (A), R4.1
unnamed: D7.4 (DIN), R30.1
unnamed: D8.2 (A), R8.2
unnamed: D9.2 (A), R7.2
unnamed: D14.2 (A), R28.2
unnamed: F1.1, J1.1
unnamed: J2.A5 (CC1), R10.1
unnamed: J2.B5 (CC2), R11.1
unnamed: Q2.1, R21.2, R22.2
unnamed: Q3.1, R23.2, R24.2
unnamed: TP2.1, U1.36 (RXD0)
unnamed: TP1.1, U1.37 (TXD0)
unnamed: C3.2, U2.1 (BOOT)
unnamed: R1.1, U2.6 (COMP)
unnamed: R3.2, U2.3 (ROSC)
unnamed: C5.2, U2.4 (SS)
unnamed: C21.1, R16.2, U5.4 (AIN0)
unnamed: C22.2, R15.2, U5.5 (AIN1)
unnamed: R17.2, U6.1 (G)
unnamed: R18.2, U7.1 (G)
unnamed: C27.1, C30.1, U8.8 (5VOUT)
unnamed: R26.1, U8.23 (BRA)
unnamed: R25.1, U8.27 (BRB)
unnamed: C29.2, U8.5 (CPI)
unnamed: C29.1, U8.4 (CPO)
PGATE-0: R21.1, U1.10 (IO17)
PGATE-1: R23.1, U1.11 (IO18)
PUMP0-N: D12.2 (A), J6.2, Q2.2
PUMP1-N: D13.2 (A), J7.2, Q3.2
S3-RX: R27.1, U1.8 (IO15), U8.14 (PDN_UART)
S3-SCL: J5.2, R13.2, U1.38 (IO2), U5.10 (SCL)
S3-SDA: J5.3, R12.1, U1.39 (IO1), U5.9 (SDA)
S3-TX: R27.2, U1.7 (IO7)
SGATE-0: R17.1, R19.2, U1.21 (IO13)
SGATE-1: R18.1, R20.2, U1.20 (IO12)
STEP: U1.5 (IO5), U8.16 (STEP)
SVDD0: C23.1, J3.1, U6.3 (D)
SVDD1: C24.1, J4.1, U7.3 (D)
USB_D+: J2.A6 (D+), J2.B6 (D+), U1.14 (IO20)
USB_D-: J2.A7 (D-), J2.B7 (D-), U1.13 (IO19)

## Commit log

2025-07-30 add schematic diagram
2025-07-30 add schematic v1
    [home-automation-sys.kicad_sch]
2025-07-30 add schematic v2
2025-07-31 add schematic v3
2025-08-11 add schematic v4
2025-08-11 add v4 schematic
2025-08-17 app backend, arduino dir init
2025-08-29 add schematic v5
2025-08-29 add gerbers and pos
    ignore BOM here
2025-10-03 add img
    [home-automation-sys.kicad_pcb, home-automation-sys.kicad_sch, homectrl-bom.csv]
2025-10-03 add power image
2025-11-23 implement testing
    [home-automation-sys.kicad_sch]
2025-12-23 lux module schematic
    [home-automation-sys.kicad_pcb, home-automation-sys.kicad_sch, homectrl-bom.csv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]
2025-12-24 setup schematic hiearchy
    [ESP-breakout.kicad_sch, actuation-module.kicad_sch, homectrl-rB.kicad_sch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]
2025-12-29 finish lux moudle/ALS
    [lux-module.kicad_pcb, lux-module.kicad_sch]
2025-12-29 power circuitry
    [ESP-breakout.kicad_sch, LM3940IMP-3.3_NOPB.step, TPS5405DR.step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]
2025-12-29 assign footprints
    [1210L110_16WR.stp, ESP-breakout.kicad_sch, power-module.kicad_sch]
2025-12-30 pmux & breakout circuitry
    [ESP-breakout.kicad_sch, power-module.kicad_sch]
2025-12-30 sensing circuitry
    [ESP-breakout.kicad_sch, IN-PI33TBTPRPGPB.step, TO-236_VIS.step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]
2025-12-31 stepper driver circuitry
    [ESP-breakout.kicad_sch, QFN28_5X5_TRI.step, actuation-module.kicad_sch]
2026-01-03 layout work
    [ESP-breakout.kicad_sch, VLS3015CX-220M-1.step, actuation-module.kicad_sch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]
2026-01-04 routing work
    [ESP-breakout.kicad_sch, homectrl-rB.kicad_pcb]
2026-01-05 more routing work
    [ESP-breakout.kicad_sch, homectrl-rB.kicad_pcb]
2026-01-06 more more routing routing work work
    [ESP-breakout.kicad_sch, homectrl-rB.kicad_pcb]
2026-01-07 silkscreen, review work
    [homectrl-rB.kicad_pcb]
2026-01-07 switch commit
    [homectrl-rB.kicad_pcb]
2026-01-07 back silkscreen
    [homectrl-rB.kicad_pcb]
2026-01-07 fix some text stuff
    [homectrl-rB.kicad_pcb, lux-module.kicad_pcb]
2026-01-07 getting there
    [homectrl-rB.kicad_pcb]
2026-01-08 add new caps, add ferrite bead, add MPNs
    [EEEFK1V101P.step, ESP-breakout.kicad_sch, MPZ2012S221AT000.step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]
2026-01-10 add MPNs and review circuits
    [0ZCG0260BF2B.step, 1210L110_16WR.stp, EEH-ZK1V101XP.step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]
2026-01-11 review, add vias & ground pour
    [homectrl-rB.kicad_pcb, lux-module.kicad_pcb, lux-module.kicad_sch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]
2026-01-11 finalizing changes
    [homectrl-rB.kicad_pcb]
2026-01-13 pad clearance & BOM fixes
    [ESP-breakout.kicad_sch, actuation-module.kicad_sch, lux-module.kicad_pcb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]
2026-01-16 swap connector in progress
    [ESP-breakout.kicad_sch, S02B-PASK-2.stp, S03B-PASK-2_LF__SN_.stp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]
2026-01-16 changes for connector revision
    [homectrl-rB.kicad_pcb]
2026-01-17 connector fixes
    [actuation-module.kicad_sch, homectrl-rB.kicad_pcb, lux-module.kicad_pcb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]
2026-01-17 more conn changes
    [homectrl-rB.kicad_pcb]
2026-01-20 add AGND, more layout work
    [homectrl-rB.kicad_pcb]
2026-01-22 BOM fix
    [ESP-breakout.kicad_sch, actuation-module.kicad_sch, power-module.kicad_sch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]
2026-02-05 silkscreen chantges
    [homectrl-rB.kicad_pcb]
2026-02-11 update ALS
    [lux-module.kicad_pcb, lux-module.kicad_sch]
2026-06-11 init r2
    [EEH-ZK1V101XP.step, ESP32-S3-WROOM-1-N8R2--3DModel-STEP-56544.STEP, S02B-PASK-2.stp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]
2026-06-12 sch work
    [homectrl-v2.kicad_sch]
2026-06-13 entry circuits
    [homectrl-v2.kicad_sch]
2026-06-14 peirpheral circuit work
    [homectrl-v2.kicad_sch]
2026-06-14 tmc2209 wiring
    [homectrl-v2.kicad_sch]
2026-06-14 power calculations
    [ETQP3M100HFN.step, SMT-0540-S-R.step, homectrl-v2.kicad_pcb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]
2026-06-15 power layout
    [homectrl-v2.kicad_pcb, homectrl-v2.kicad_sch]
2026-06-15 fet fix
    [homectrl-v2.kicad_pcb, homectrl-v2.kicad_sch]
2026-06-15 experimenting w connectors
    [homectrl-v2.kicad_pcb, homectrl-v2.kicad_sch]
2026-06-15 connectot placement
    [homectrl-v2.kicad_pcb]
2026-06-16 power routing
    [homectrl-v2.kicad_pcb, homectrl-v2.kicad_sch]
2026-06-16 actuator routes
    [homectrl-v2.kicad_pcb]
2026-06-17 misc work
    [homectrl-v2.kicad_sch]
2026-06-17 start signal routes
    [homectrl-v2.kicad_pcb]
2026-06-17 more signal routing
    [homectrl-v2.kicad_pcb, homectrl-v2.kicad_sch]
2026-06-17 finish component routing
    [homectrl-v2.kicad_pcb, homectrl-v2.kicad_sch]
2026-06-17 logic power routing
    [homectrl-v2.kicad_pcb, homectrl-v2.kicad_sch]
2026-06-18 board outline done
    [homectrl-v2.kicad_pcb]
2026-06-19 reroute esp pins
    [homectrl-v2.kicad_pcb]
2026-06-19 wrapping up layout & routing
    [CMT-0525-75-SMT-TR.step, homectrl-v2.kicad_pcb, homectrl-v2.kicad_sch]
2026-06-19 added part numbers
    [homectrl-v2.kicad_sch]
2026-06-20 start silkscreen
    [homectrl-v2.kicad_pcb]
2026-06-22 add models
    [container_base.step, container_lid.step, homectrl_v2_board_outline.dxf]
2026-06-28 add imgs
    [homectrl-v2.kicad_sch]
2026-06-30 pump drivers
    [homectrl-v2.kicad_sch]
